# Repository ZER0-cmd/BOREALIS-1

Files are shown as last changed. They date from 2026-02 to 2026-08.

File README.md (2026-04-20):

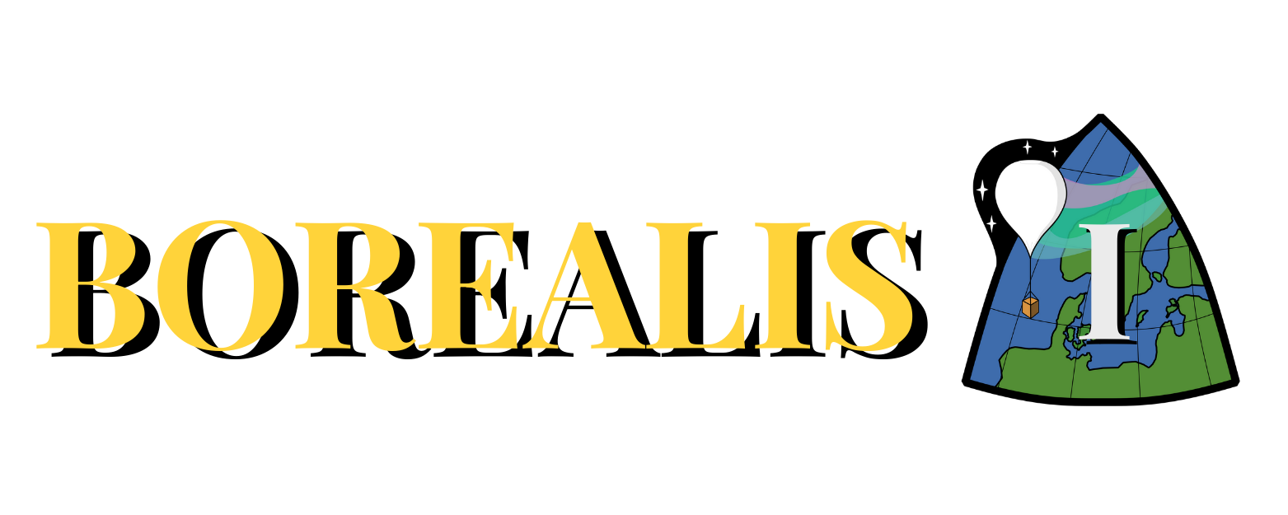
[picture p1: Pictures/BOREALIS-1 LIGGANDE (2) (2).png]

# Från klassrummen till rymden, en röd tråd från nyfikenhet till framtidens ingenjörer!
BOREALIS är ett projekt för högstadieelever som syftar till att introducera unga till teknik och rymdforskning genom praktiska, rymdnära experiment anpassade till deras kunskapsnivå. Genom att designa och bygga små experiment som skickas upp med stratosfäriska ballonger får eleverna uppleva ett verkligt rymdprojekt, vilket ger dem en första inblick i rymdteknik och ingenjörskonst. Projektet är utformat för att passa den grundläggande förståelse för naturvetenskap som elever på högstadiet har, och fungerar som en inspirerande introduktion till STEM-ämnen och framtida rymdrelaterade projekt.

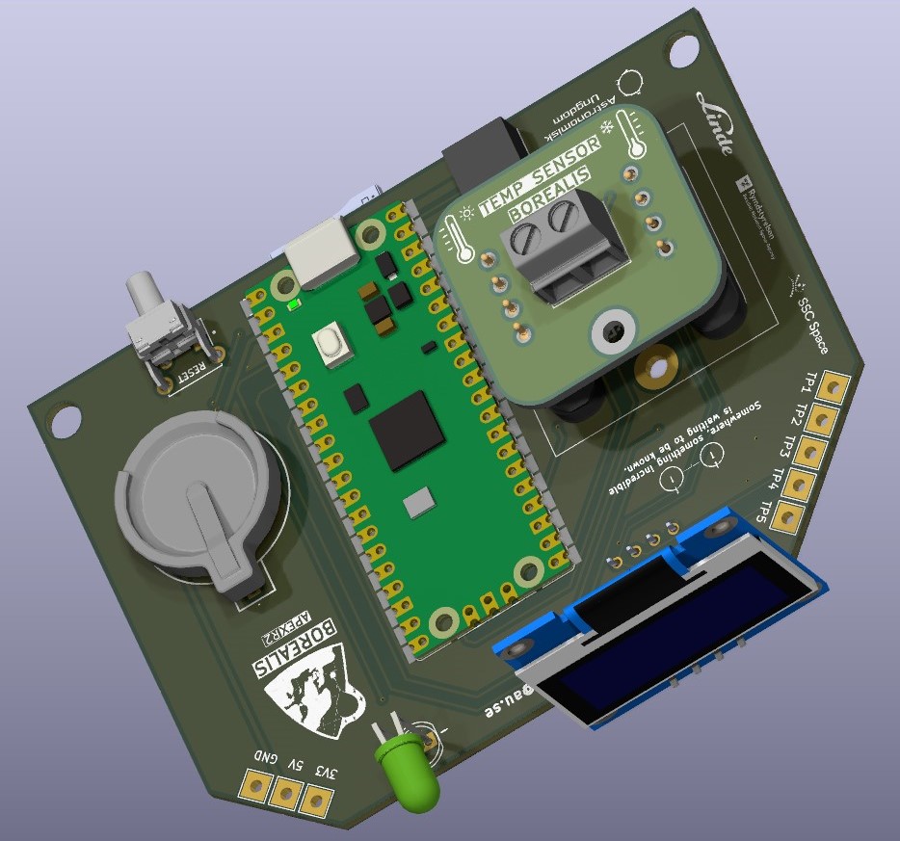
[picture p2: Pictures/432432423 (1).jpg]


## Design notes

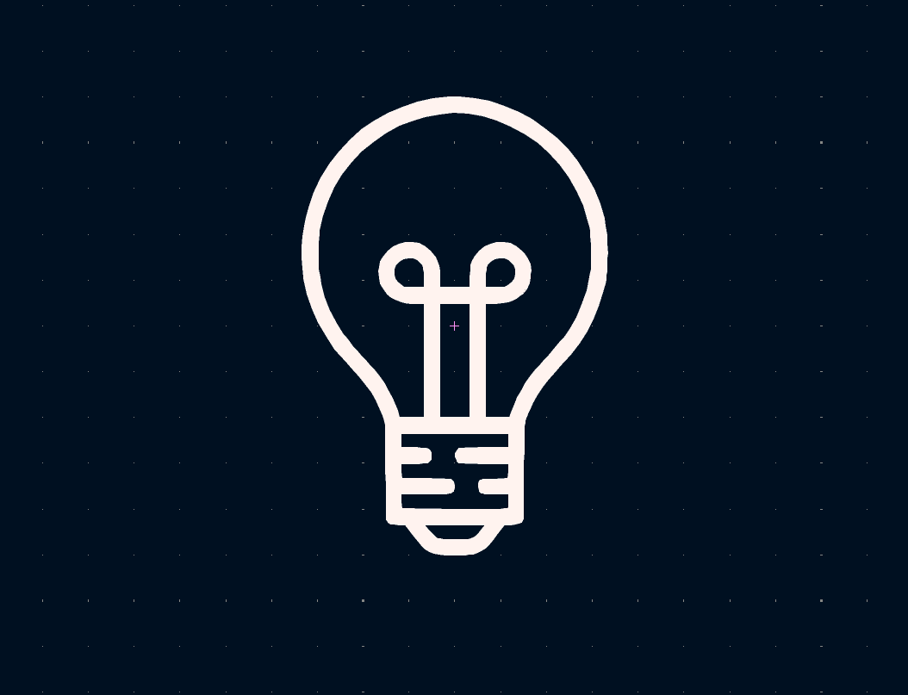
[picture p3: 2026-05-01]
Pictures/Internal/Light sensor.png

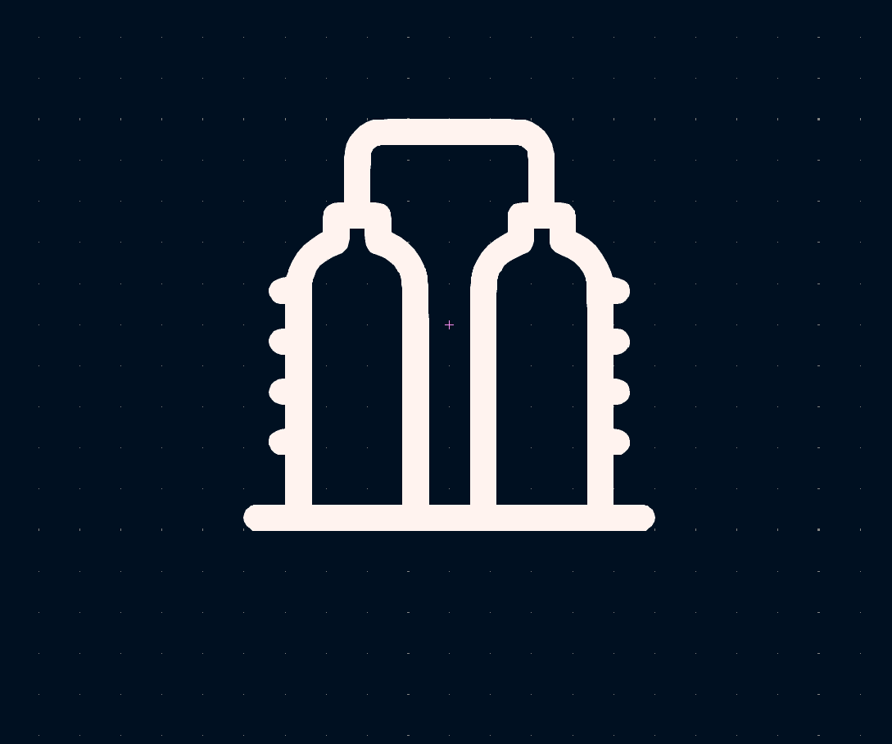
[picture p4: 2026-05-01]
Pictures/Internal/Gas sensor.png

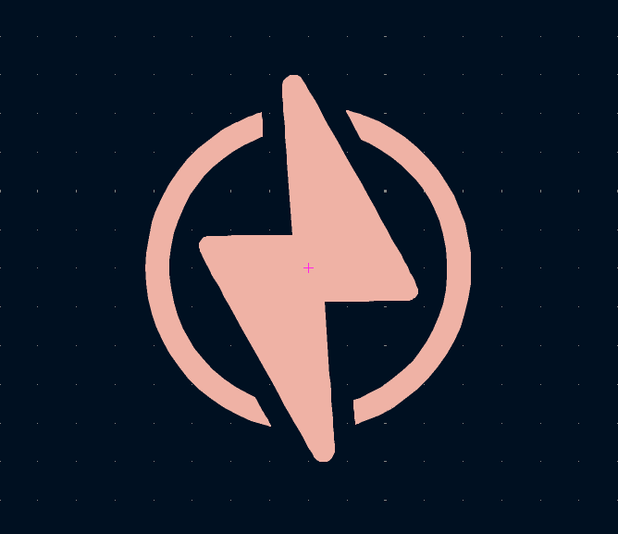
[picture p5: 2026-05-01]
Pictures/Internal/Solar panel.png

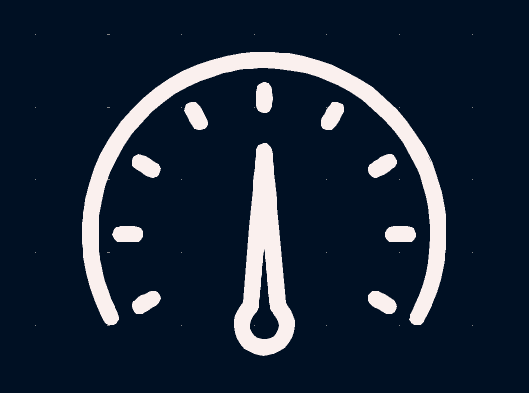
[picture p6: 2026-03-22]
Pictures/Internal/Barometer.png

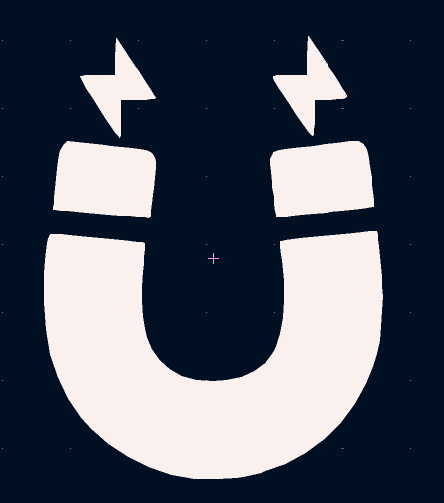
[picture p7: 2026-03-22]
Pictures/Internal/Magnetometer.png

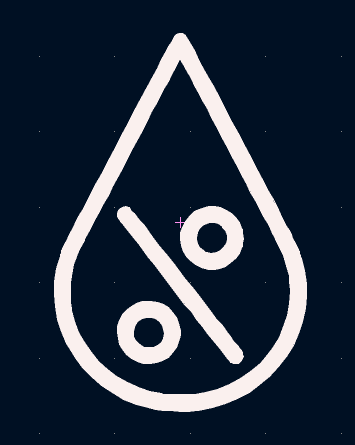
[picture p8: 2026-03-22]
Pictures/Internal/Humidity sensor.png

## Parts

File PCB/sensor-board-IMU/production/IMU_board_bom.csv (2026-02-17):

Designator | Footprint | Quantity | Value | LCSC Part #
C1, C5 | 0805 | 2 | 0.1uF
C2 | 0805 | 1 | 10nF
MPU6500 | mpu6500 | 1 | ~
R1 | 0805 | 1 | R
R2, R3 | 0805 | 2 | 4.7k
U1, U2 | MAGNETIC POGO CONN. | 2 | MAGNETIC POGO CONN.

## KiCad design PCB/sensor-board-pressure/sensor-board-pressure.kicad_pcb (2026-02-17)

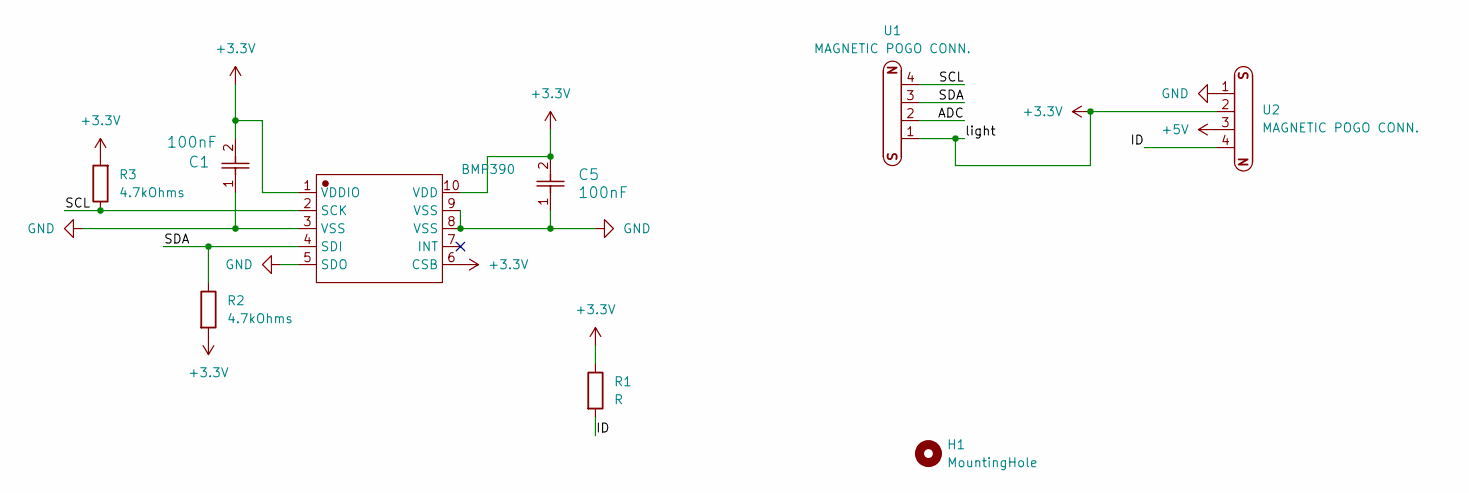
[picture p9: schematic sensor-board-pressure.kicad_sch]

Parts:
BMP390: BMP388
C1, C5: 100nF; C_0805_2012Metric
H1: MountingHole; MountingHole_2.7mm_M2.5_Pad
R1: R; R_0805_2012Metric
R2, R3: 4.7kOhms; R_0805_2012Metric
U1, U2: MAGNETIC POGO CONN.

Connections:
+3.3V: BMP390.1 (VDDIO), BMP390.6 (CSB), BMP390.10 (VDD), C1.2, C5.2, R1.1, R2.2, R3.2, U1.1, U2.2
+5V: U2.3
/ADC: U1.2
/ID: R1.2, U2.4
/SCL: BMP390.2 (SCK), R3.1, U1.4
/SDA: BMP390.4 (SDI), R2.1, U1.3
GND: BMP390.3 (VSS), BMP390.5 (SDO), BMP390.8 (VSS), BMP390.9 (VSS), C1.1, C5.1, U2.1

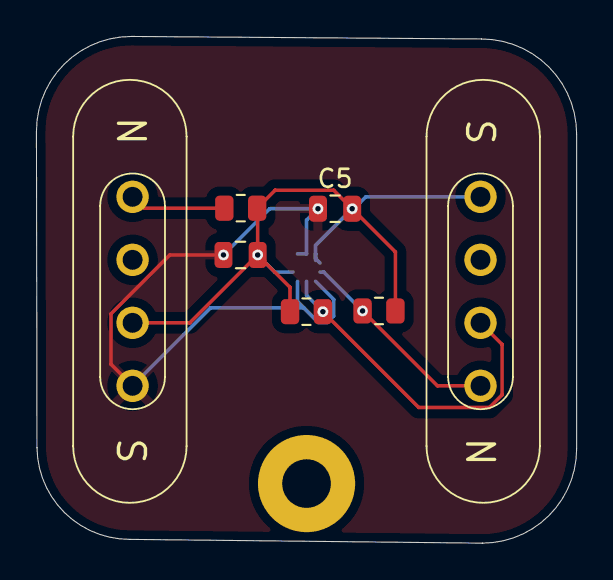
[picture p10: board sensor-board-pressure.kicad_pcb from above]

Board: 2 copper layers, 30.0 x 28.1 mm, 9 parts (1 on the bottom side), 5 nets.

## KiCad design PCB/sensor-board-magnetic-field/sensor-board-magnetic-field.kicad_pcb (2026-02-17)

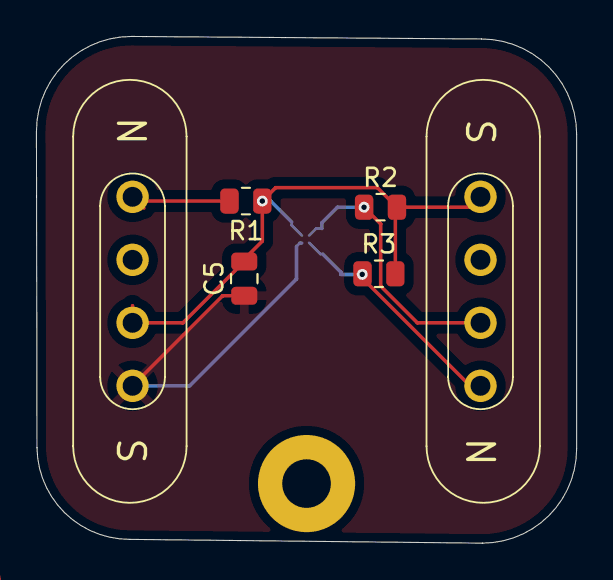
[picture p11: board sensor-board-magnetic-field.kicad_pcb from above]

Board: 2 copper layers, 30.0 x 28.1 mm, 8 parts (1 on the bottom side), 5 nets.

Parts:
C5: 2.2uf; C_0805_2012Metric
H1: MountingHole; MountingHole_2.7mm_M2.5_Pad
MMC5603NJ1: XDCR_MMC5603NJ
R1: R; R_0805_2012Metric
R2, R3: 2.7k; R_0805_2012Metric
U1, U2: MAGNETIC POGO CONN.

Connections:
+3.3V: C5.2, MMC5603NJ1.B1 (VDD), R1.1, R2.2, R3.2, U1.1, U2.2
/ID: R1.2, U2.4
/SCL: MMC5603NJ1.A2 (SCL), R3.1, U1.4
/SDA: MMC5603NJ1.B2 (SDA), R2.1, U1.3
GND: C5.1, MMC5603NJ1.A1 (VSA), U2.1

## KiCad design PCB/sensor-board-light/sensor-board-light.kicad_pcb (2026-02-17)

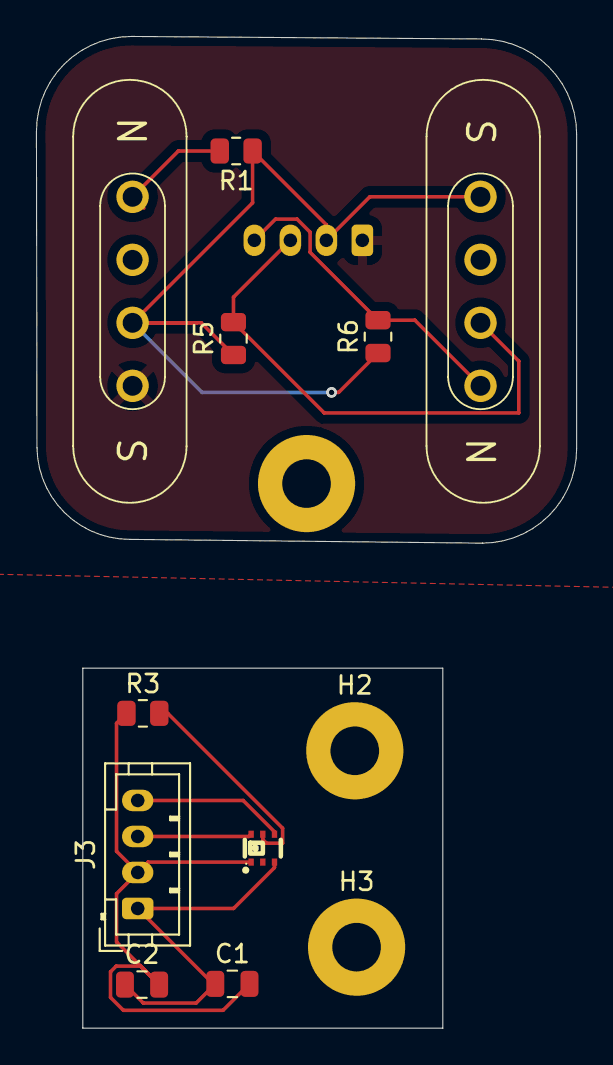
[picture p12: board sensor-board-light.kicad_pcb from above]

Board: 2 copper layers, 30.0 x 55.1 mm, 14 parts (1 on the bottom side), 9 nets.

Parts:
C1: 0.1uF; C_0805_2012Metric
C2: 4.7uF; C_0805_2012Metric
H1, H2, H3: MountingHole; MountingHole_2.7mm_M2.5_Pad
J1, J3: Conn_01x04_Pin; JST_PH_B4B-PH-K_1x04_P2.00mm_Vertical
LTR-390UV-01: SENSOR-SMD_LTR-390UV-01
R1: R; R_0805_2012Metric
R3, R5, R6: 10k; R_0805_2012Metric
U1, U2: MAGNETIC POGO CONN.

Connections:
+3.3V: J1.2, R1.1, R5.1, R6.1, U1.1, U2.2
/3.3v: C1.2, C2.2, J3.2, LTR-390UV-01.1 (VDD), R3.1
/ID: R1.2, U2.4
/SCL: J1.4, R6.2, U1.4
/SCL1: J3.4, LTR-390UV-01.4 (SCL)
/SDA: J1.3, R5.2, U1.3
/SDA1: J3.3, LTR-390UV-01.6 (SDA)
GND: C1.1, C2.1, J1.1, J3.1, LTR-390UV-01.3 (GND), U2.1
unnamed: LTR-390UV-01.5 (INT), R3.2

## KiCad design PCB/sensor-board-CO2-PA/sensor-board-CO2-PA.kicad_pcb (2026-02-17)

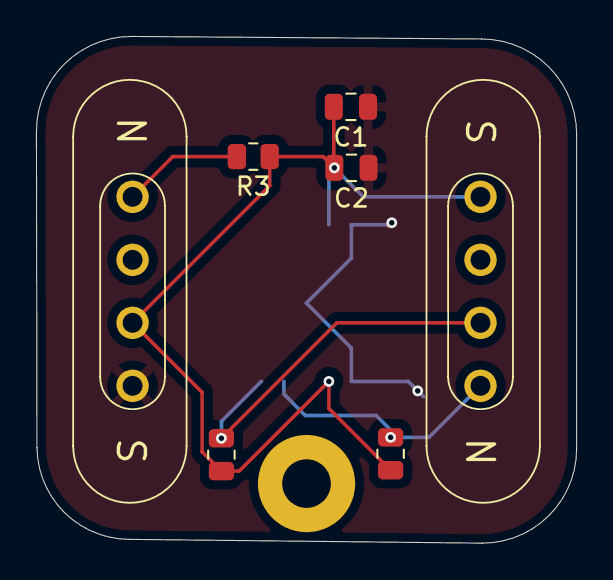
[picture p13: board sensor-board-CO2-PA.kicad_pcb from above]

Board: 2 copper layers, 30.0 x 28.2 mm, 9 parts (1 on the bottom side), 5 nets.

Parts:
C1: 10microf; C_0805_2012Metric
C2: 0.1uf; C_0805_2012Metric
H1: MountingHole; MountingHole_2.7mm_M2.5_Pad
R1: 10K; R_0805_2012Metric
R2: 10k; R_0805_2012Metric
R3: R; R_0805_2012Metric
U1, U2: MAGNETIC POGO CONN.
U1#2: SCD40-D-R2; SCD40 footprint

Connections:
+3.3V: C1.2, C2.2, R1.1, R2.1, R3.1, U1.1, U1#2.7 (VDD), U1#2.19 (VDDH), U2.2
/ID: R3.2, U2.4
/SCL: R2.2, U1.4, U1#2.9 (SCL)
/SDA: R1.2, U1.3, U1#2.10 (SDA)
GND: C1.1, C2.1, U1#2.6 (GND), U1#2.20 (GND), U1#2.21 (GND), U2.1

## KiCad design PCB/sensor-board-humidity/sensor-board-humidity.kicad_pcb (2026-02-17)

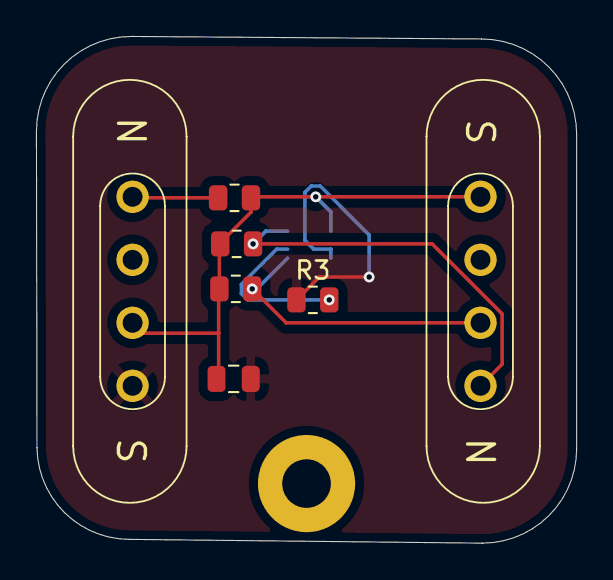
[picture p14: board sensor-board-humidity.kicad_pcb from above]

Board: 2 copper layers, 30.0 x 28.1 mm, 9 parts (1 on the bottom side), 6 nets.

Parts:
C5: 100nf; C_0805_2012Metric
H1: MountingHole; MountingHole_2.7mm_M2.5_Pad
R1: R; R_0805_2012Metric
R3, R4, R5: 10k; R_0805_2012Metric
SHT31: sht31-footprint
U1, U2: MAGNETIC POGO CONN.

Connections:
+3.3V: C5.1, R1.1, R4.1, R5.2, SHT31.5 (VDD), U1.1, U2.2
/ID: R1.2, U2.4
/SCL: R4.2, SHT31.4 (SCL), U1.4
/SDA: R5.1, SHT31.1 (SDA), U1.3
GND: C5.2, R3.1, SHT31.7 (R), SHT31.8 (VSS), SHT31.9 (EP), U2.1
unnamed: R3.2, SHT31.2 (ADDR)

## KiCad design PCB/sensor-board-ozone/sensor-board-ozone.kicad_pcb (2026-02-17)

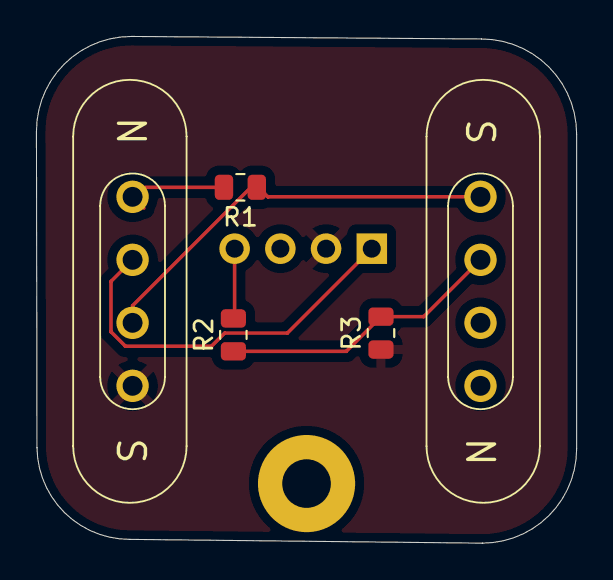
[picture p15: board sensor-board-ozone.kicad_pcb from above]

Board: 2 copper layers, 30.0 x 28.2 mm, 7 parts (1 on the bottom side), 6 nets.

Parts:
H1: MountingHole; MountingHole_2.7mm_M2.5_Pad
J2: Conn_01x04_Pin (MQ series sensor. 4pins (5v, gnd,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; PinHeader_1x04_P2.54mm_Vertical
R1, R2, R3: R; R_0805_2012Metric
U1, U2: MAGNETIC POGO CONN.

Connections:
+3.3V: R1.1, U1.1, U2.2
+5V: J2.1, U2.3
/ADC: R2.1, R3.2, U1.2
/ID: R1.2, U2.4
GND: J2.2, R3.1, U2.1
unnamed: J2.4, R2.2

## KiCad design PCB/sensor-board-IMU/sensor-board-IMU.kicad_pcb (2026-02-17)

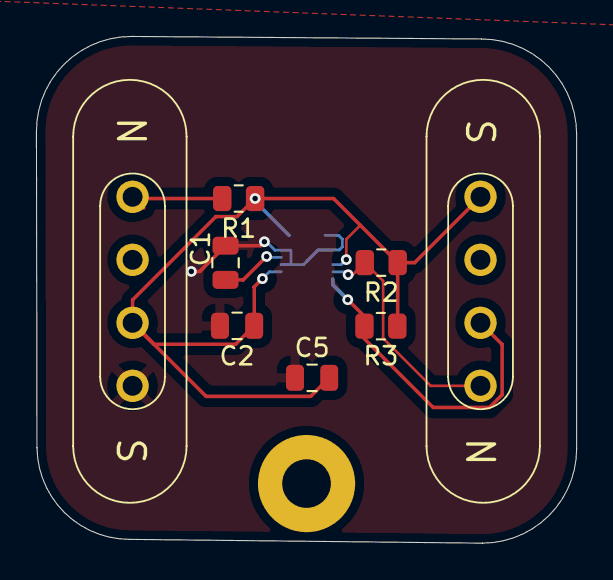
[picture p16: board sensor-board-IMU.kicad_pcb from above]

Board: 2 copper layers, 30.0 x 28.1 mm, 10 parts (1 on the bottom side), 6 nets.

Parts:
C1: 0.1uF; C_0805_2012Metric
C2: 10nF; C_0805_2012Metric
C5: 0.1uf; C_0805_2012Metric
H1: MountingHole; MountingHole_2.7mm_M2.5_Pad
MPU6500: mpu6500
R1: R; R_0805_2012Metric
R2, R3: 4.7k; R_0805_2012Metric
U1, U2: MAGNETIC POGO CONN.

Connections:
+3.3V: C2.1, C5.2, MPU6500.8 (VDDIO), MPU6500.13 (VDD), MPU6500.22 (nCS), R1.1, R2.1, R3.1, U1.1, U2.2
/ID: R1.2, U2.4
/SCL: MPU6500.23 (SCL/SCLK), R2.2, U1.4
/SDA: MPU6500.24 (SDA/SDI), R3.2, U1.3
GND: C1.2, C2.2, C5.1, MPU6500.9 (SDO/AD0), MPU6500.11 (FSYNC), MPU6500.18 (GND), MPU6500.20 (RESV), MPU6500.25 (EP), U2.1
unnamed: C1.1, MPU6500.10 (REGOUT)

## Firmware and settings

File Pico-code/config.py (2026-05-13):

# config.py - central hardware + app settings for Pico project

# OLED
OLED_WIDTH = 128
OLED_HEIGHT = 64
OLED_I2C_ADDR = 0x3C
OLED_SPLASH_MS = 3000

# OLED / RTC bus
# GP0 = SDA, GP1 = SCL
I2C_ID = 0
I2C_SDA = 0
I2C_SCL = 1
I2C_FREQ = 400_000

# DS1302 RTC (3-wire serial: CLK, DAT, CE)
# Assign to free GPIO pins on your board
DS1302_CLK = 20
DS1302_DAT = 21
DS1302_CE  = 22

# microSD detect
SD_DETECT_PIN = 19
SD_DETECT_ACTIVE_LOW = True

# Button / switch
BUTTON_PIN = 15
BUTTON_PULL = "down"
BUTTON_ACTIVE_LEVEL = 1
BUTTON_DEBOUNCE_MS = 50

# One status LED
STATUS_LED_PIN = 2
LED_ACTIVE_HIGH = True

# SD Card (SPI1)
SD_SPI_ID = 1
SD_SCK = 10
SD_MOSI = 11 #RX
SD_MISO = 8 #TX
SD_CS = 9
SD_BAUDRATE = 1_000_000
SD_MOUNT_POINT = "/sd"

# Sampling / UI update
SAMPLE_INTERVAL_MS = 1000

# Sensor identification ADC
SENSOR_ID_ADC_PIN = 28

# Sensor bus (from your working test scripts)
SENSOR_I2C_ID = 1
SENSOR_I2C_SDA = 14
SENSOR_I2C_SCL = 15
SENSOR_I2C_FREQ = 100_000

# ADC bus (i2c0 on schematic)
ADC_I2C_ID = 0
ADC_I2C_SDA = 0
ADC_I2C_SCL = 1
ADC_I2C_FREQ = 400_000
ADC_CHANNEL = 2


# CO2 | 680 Ω
# BAR | 510 Ω
# light | 750 Ω
# GAS | 560 Ω
# HUM | 1.1 kΩ
# VOLT | 820 Ω
# TEMP | 1.2 kΩ
# MAG | 910 Ω
# ACL | 620 Ω

# Formula:
# V = 6.6e7 / (R + 1000)

# Sensor ID ranges
SENSOR_NONE_ID = 0
SENSOR_CO2_ID = 39355
SENSOR_PRESSURE_ID = 43354
SENSOR_LIGHT_ID = 37800
SENSOR_GAS_ID = 42314
SENSOR_HUMIDITY_ID = 31518
SENSOR_SOLAR_ID = 36263
SENSOR_TEMP_ID = 30136
SENSOR_MAGNETOMETER_ID = 34645
SENSOR_MPU6500_ID = 40841

UV_RESOLUTION = 18

# Timing
SENSOR_ANNOUNCE_MS = 2000
SENSOR_READ_INTERVAL_MS = 1000

# Reset pin
RESET1_PIN = 17
RESET2_PIN = 6

DEFAULT_FILE_NAME = 'data.csv'

LED_GREEN = 3
LED_BLUE = 4

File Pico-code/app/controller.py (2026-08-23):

import time
from machine import Pin, I2C, SPI, reset
import config
from drivers.display_ssd1306 import SSD1306_I2C
from drivers.output_led import LED
from drivers.sd_detect import SdDetect
from app.timekeeping import Timekeeper
from app.ui import Ui
from app import logging
from app.sensor_manager import (
    SensorManager,
    SENSOR_NONE,
    SENSOR_HUMIDITY,
    SENSOR_PRESSURE,
    SENSOR_MPU6500,
    SENSOR_UNKNOWN,
    SENSOR_GAS,
    SENSOR_LIGHT,
    SENSOR_SOLAR,
    SENSOR_TEMP,
    SENSOR_MAGNET,
    SENSOR_NAMES,
)


class Core(Timekeeper):
    def __init__(self):
        self.green_led = LED(
            config.LED_GREEN,
            active_high=config.LED_ACTIVE_HIGH,
        )
        self.blue_led = LED(
            config.LED_BLUE,
            active_high=config.LED_ACTIVE_HIGH,
        )
        self.status_led = LED(
            config.STATUS_LED_PIN,
            active_high=config.LED_ACTIVE_HIGH,
        )
        self.reset1 = Pin(config.RESET1_PIN, Pin.IN, Pin.PULL_DOWN)
        self.reset2 = Pin(config.RESET2_PIN, Pin.IN, Pin.PULL_DOWN)
        self.i2c = I2C(
            config.I2C_ID,
            sda=Pin(config.I2C_SDA),
            scl=Pin(config.I2C_SCL),
            freq=config.I2C_FREQ,
        )
        self.oled = None
        self.sd_detect = SdDetect(
            config.SD_DETECT_PIN,
            active_low=config.SD_DETECT_ACTIVE_LOW,
        )
        self.sd = None
        self.sensor_manager = SensorManager(i2c_adc=self.i2c)
        self.last_sensor_read_ms = 0
        self.log_ready = False
        self.data = {}
        self.datakeys = []
        self.sensorkeys = []
        self.ui = None
        self.filter = []

        self.dataready = False

        Timekeeper.__init__(self)

    def _run_startup_checks(self):
        start_ms = time.ticks_ms()
        splash_ms = config.OLED_SPLASH_MS
        led_state = False
        last_toggle_ms = start_ms
        blink_interval_ms = 100
        sd_ok = False
        while time.ticks_diff(time.ticks_ms(), start_ms) < splash_ms:
            now = time.ticks_ms()
            sd_ok = self.sd_detect.is_inserted()
            if time.ticks_diff(now, last_toggle_ms) >= blink_interval_ms:
                last_toggle_ms = now
                led_state = not led_state
                if led_state:
                    self.status_led.on()
                else:
                    self.status_led.off()
            time.sleep_ms(10)
        return sd_ok

    def _show_check_result(self, ok):
        if ok:
            self.status_led.off()
            time.sleep_ms(80)
            self.status_led.on()
            time.sleep_ms(200)
            self.status_led.off()
            time.sleep_ms(120)
            self.status_led.on()
        else:
            self.status_led.off()

    def _oledmanager(self):
        if self.ui is not None:
            self.oled = self.ui.oled
        if self.oled is not None:
            return
        if config.OLED_I2C_ADDR in self.i2c.scan():
            try:
                self.oled = SSD1306_I2C(
                    config.OLED_WIDTH,
                    config.OLED_HEIGHT,
                    self.i2c,
                    addr=config.OLED_I2C_ADDR,
                )
            except Exception as e:
                print("OLED init failed:", e)
                self.oled = None
        self.ui = Ui(self.oled)
        self.oled = self.ui.oled

    def _experimentmanager(self):
        self.changed, kind, adc_value = self.sensor_manager.refresh_connection()
        if self.changed:
            if kind == SENSOR_NONE:
                self.ui.show_sensor_disconnected()
                self.ui.show()
                time.sleep_ms(config.SENSOR_ANNOUNCE_MS)
            elif kind == SENSOR_UNKNOWN:
                self.ui.show_unknown_sensor(adc_value)
                self.ui.show()
                time.sleep_ms(config.SENSOR_ANNOUNCE_MS)
            else:
                self.ui.show_sensor_connected(SENSOR_NAMES[kind])
                self.ui.show()
                time.sleep_ms(config.SENSOR_ANNOUNCE_MS)

            self.filter = []

        now = time.ticks_ms()
        if time.ticks_diff(now, self.last_sensor_read_ms) >= config.SENSOR_READ_INTERVAL_MS:
            self.last_sensor_read_ms = now
            self.data = self.sensor_manager.read_data()
            if self.data is None:
                self.ui.show_sensor_disconnected()
                self.dataready = False
                return
            if self.data["kind"] == SENSOR_HUMIDITY:
                self.sensorkeys = ["humidity_percent"]
                show = self.ui.show_humidity_data
            elif self.data["kind"] == SENSOR_PRESSURE:
                self.sensorkeys = ["pressure_hpa"]
                show = self.ui.show_pressure_data
            elif self.data["kind"] == SENSOR_MPU6500:
                self.sensorkeys = ["ax_g", "ay_g", "az_g", "gx_dps", "gy_dps", "gz_dps"]
                show = self.ui.show_mpu6500_data
            elif self.data["kind"] == SENSOR_SOLAR:
                self.sensorkeys = ["voltage"]
                show = self.ui.show_solar_data
            elif self.data["kind"] == SENSOR_TEMP:
                self.sensorkeys = ["temperature_c"]
                show = self.ui.show_temp_data
            elif self.data["kind"] == SENSOR_GAS:
                self.sensorkeys = ["alcohol"]
                show = self.ui.show_gas_data
            elif self.data["kind"] == SENSOR_LIGHT:
                self.sensorkeys = ["uvindex"]
                show = self.ui.show_light_data
            elif self.data["kind"] == SENSOR_MAGNET:
                self.sensorkeys = ["B_x", "B_y", "B_z"]
                show = self.ui.show_magnet_data
            else:
                self.ui.show_unknown_sensor(self.data["adc"])
                self.dataready = False
                return

            self.data["elapsed_s"] = self.elapsed_s()
            self.data['datetime'] = self.fdate()
            self.datakeys = ['datetime', "elapsed_s"] + self.sensorkeys
            if self.filter == []:
                self.filter = self.sensorkeys

            if self.cdata is not None:
                kind = self.data["kind"]
                if kind in self.cdata:
                    c = self.cdata[kind]
                    for k, (scale, shift) in c.items():
                        if k in self.data:
                            self.data[k] = self.data[k] * scale + shift

            show(*(self.data[k] for k in self.sensorkeys))

            self.dataready = True
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

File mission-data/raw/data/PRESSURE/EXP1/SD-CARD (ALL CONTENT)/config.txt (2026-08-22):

# For more options and information see
# http://rptl.io/configtxt
# Some settings may impact device functionality. See link above for details

# Uncomment some or all of these to enable the optional hardware interfaces
#dtparam=i2c_arm=on
#dtparam=i2s=on
dtparam=spi=on

# Enable audio (loads snd_bcm2835)
dtparam=audio=on

# Additional overlays and parameters are documented
# /boot/firmware/overlays/README

# Automatically load overlays for detected cameras
camera_auto_detect=1

# Automatically load overlays for detected DSI displays
display_auto_detect=1

# Automatically load initramfs files, if found
auto_initramfs=1

# Enable DRM VC4 V3D driver
dtoverlay=vc4-kms-v3d
max_framebuffers=2

# Don't have the firmware create an initial video= setting in cmdline.txt.
# Use the kernel's default instead.
disable_fw_kms_setup=1

# Run in 64-bit mode
arm_64bit=1

# Disable compensation for displays with overscan
disable_overscan=1

# Run as fast as firmware / board allows
arm_boost=1

[cm4]
# Enable host mode on the 2711 built-in XHCI USB controller.
# This line should be removed if the legacy DWC2 controller is required
# (e.g. for USB device mode) or if USB support is not required.
otg_mode=1

[cm5]
dtoverlay=dwc2,dr_mode=host

[pi5]
dtoverlay=nospi10

[all]
enable_uart=1

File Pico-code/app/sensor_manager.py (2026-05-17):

from machine import ADC, Pin, I2C
import time
import config
import gc

from drivers.sensor_sht31 import SHT31

from drivers.bmp390 import BMP390
from drivers.mpu6500 import MPU6500
from drivers.ADS1115 import ADS1115
from drivers.mmc5603 import MMC5603
from drivers import ltr390


SENSOR_NONE = config.SENSOR_NONE_ID
SENSOR_CO2 = config.SENSOR_CO2_ID
SENSOR_HUMIDITY = config.SENSOR_HUMIDITY_ID
SENSOR_PRESSURE = config.SENSOR_PRESSURE_ID
SENSOR_MPU6500 = config.SENSOR_MPU6500_ID
SENSOR_LIGHT = config.SENSOR_LIGHT_ID 
SENSOR_GAS = config.SENSOR_GAS_ID
SENSOR_SOLAR = config.SENSOR_SOLAR_ID
SENSOR_TEMP = config.SENSOR_TEMP_ID
SENSOR_MAGNET = config.SENSOR_MAGNETOMETER_ID
SENSOR_UNKNOWN = "unknown"

SENSOR_NAMES = {
    SENSOR_NONE : "No sensor",
    SENSOR_HUMIDITY : 'Humidity sensor',
    SENSOR_PRESSURE : 'Barometer',
    SENSOR_MPU6500 : 'Accelerometer',
    SENSOR_LIGHT : 'Light sensor',
    SENSOR_GAS : 'Gas sensor',
    SENSOR_SOLAR : 'Solar panel',
    SENSOR_TEMP : 'Termometer',
    SENSOR_CO2 : 'CO2 sensor',
    SENSOR_MAGNET : 'Magnetometer',
    SENSOR_UNKNOWN : "Unknown sensor"
}

class SensorManager:
    def __init__(self, i2c_adc=None):
        self.adc = ADC(config.SENSOR_ID_ADC_PIN)

        self.i2c = I2C(
            config.SENSOR_I2C_ID,
            sda=Pin(config.SENSOR_I2C_SDA),
            scl=Pin(config.SENSOR_I2C_SCL),
            freq=config.SENSOR_I2C_FREQ,
        )

        if i2c_adc is not None:
            self.i2c_adc = i2c_adc
        else:
            self.i2c_adc = I2C(
                config.ADC_I2C_ID,
                sda=Pin(config.ADC_I2C_SDA),
                scl=Pin(config.ADC_I2C_SCL),
                freq=config.ADC_I2C_FREQ,
            )

        self.current_kind = None
        self.sensor = None
        self._pending = None
        self._pcount = 0

    def read_adc(self): # ID
        return self.adc.read_u16()
    
    def _adc(self): # Actual ADC
        return self.sensor.read_voltage(config.ADC_CHANNEL)
    
    @staticmethod
    def classify(adc_value):
        closest = min([SENSOR_NONE, SENSOR_GAS, SENSOR_HUMIDITY, SENSOR_LIGHT, SENSOR_MPU6500, SENSOR_PRESSURE, SENSOR_SOLAR, SENSOR_TEMP, SENSOR_CO2, SENSOR_MAGNET], key=lambda x : abs(x-adc_value))
        if abs(adc_value - closest) > 3000:
            return SENSOR_UNKNOWN
        return closest

    def connect_for_kind(self, kind):
        self.sensor = None
        self.current_kind = kind
        gc.collect()

        time.sleep_ms(20)
        if kind == SENSOR_NONE:
            return
        try:
            if kind == SENSOR_HUMIDITY:
                self.sensor = SHT31(self.i2c)
                return

            if kind == SENSOR_PRESSURE:
                last_exc = None
                for addr in (0x77, 0x76):
                    try:
                        self.sensor = BMP390(self.i2c, address=addr)
                        return
                    except Exception as e:
                        last_exc = e
                if last_exc:
                    raise last_exc
                raise RuntimeError("BMP390 not found")

            if kind == SENSOR_MPU6500:
                last_exc = None
                for addr in (0x68, 0x69):
                    try:
                        self.sensor = MPU6500(self.i2c, address=addr)
                        return
                    except Exception as e:
                        last_exc = e
                if last_exc:
                    raise last_exc
                raise RuntimeError("MPU6500 not found")
            
            if kind == SENSOR_LIGHT:
                # note: als mode exclusive with uv
                self.sensor = ltr390.LTR390(self.i2c)
                self.gain = 1
                self.sensor.set_gain(ltr390.GAINS[self.gain])
                self.sensor.set_resolution(config.UV_RESOLUTION)
                self.sensor.enable_uv()
                time.sleep_ms(self.sensor._int_ms + 10)
                return
            
            if kind == SENSOR_MAGNET:
                self.sensor = MMC5603(self.i2c)
                self.sensor.set_resolution(0)
                self.qcal = self.sensor.read_raw()
                return
            
            if kind in (SENSOR_TEMP, SENSOR_SOLAR, SENSOR_GAS):
                self.sensor = ADS1115(self.i2c_adc)
        except Exception as e:
            self.current_kind = SENSOR_UNKNOWN
            self.sensor = None

    def refresh_connection(self):
        try:
            adc_value = self.read_adc()
            kind = self.classify(adc_value)
            
            if kind == self._pending:
                self._pcount += 1
            else:
                self._pending = kind
                self._pcount = 1

            if self._pcount >= 8 and kind != self.current_kind:
                self.connect_for_kind(kind)
                return True, kind, adc_value

            return False, kind, adc_value
        except Exception:
            return False, self.current_kind, 0

    def read_data(self):
        if self.current_kind == SENSOR_NONE:
            return None
        
        if self.current_kind == SENSOR_UNKNOWN:
            return {
                "kind": SENSOR_UNKNOWN,
                "adc": self.read_adc(),
            }

        try:
            if self.current_kind == SENSOR_HUMIDITY:
                temp_c, humidity = self.sensor.read()
                return {
                    "kind": SENSOR_HUMIDITY,
                    "temperature_c": temp_c,
                    "humidity_percent": humidity,
                }

            if self.current_kind == SENSOR_PRESSURE:
                temp_c, pressure_pa = self.sensor.read()
                return {
                    "kind": SENSOR_PRESSURE,
                    "pressure_hpa": pressure_pa / 100.0,
                    "temperature_c" : temp_c
                }

            if self.current_kind == SENSOR_MPU6500:
                ax, ay, az = self.sensor.read_accel()
                gx, gy, gz = self.sensor.read_gyro()
                temp_c = self.sensor.read_temperature()

                return {
                    "kind": SENSOR_MPU6500,
                    "temperature_c": temp_c,
                    "ax_g": ax,
                    "ay_g": ay,
                    "az_g": az,
                    "gx_dps": gx,
                    "gy_dps": gy,
                    "gz_dps": gz,
                }
            
            if self.current_kind == SENSOR_TEMP:
                v = self._adc()
                temp = (v - 1.25) / 0.005
                return {
                    "kind" : SENSOR_TEMP,
                    "temperature_c" : temp
                    }

            if self.current_kind == SENSOR_GAS:
                v = self._adc()
                return {'kind': SENSOR_GAS,
                        'alcohol': 1.5*v}
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

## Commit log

2026-02-15 Update PCB files (pressure + solar)#
    [sensor-board-CO2-PA.kicad_pcb, sensor-board-pressure.kicad_pcb, sensor-board-pressure.kicad_sch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]
2026-02-16 made some changes
    [BOREALIS_MOTHERBOARD.kicad_pcb, BOREALIS_MOTHERBOARD.kicad_sch, Borealis.kicad_pcb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]
2026-02-17 Made some final checks and changes
    [IMU_board_bom.csv, IMU_board_designators.csv, IMU_board_positions.csv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]
2026-02-22 Add files via upload
    Added sample data
    [Sweden_CH4_CO2_0_32km.csv, standard_atmosphere_si_noisy_strong.csv, stockholm_solar_irradiance_0-30km_clear_noon_equinox.csv]
2026-03-07 Update module_eng.py
    Added support for inverted y and x axis
2026-03-10 Sourced new sensor libraries
2026-03-20 UI picture support
    [logo.csv]
2026-03-21 fixed picture
    [logo.csv]
2026-03-21 Actually fixed picture
    [logo.csv]
2026-03-21 LED works now!
2026-03-21 added some sensor stuff
2026-03-21 made some sensor changes
2026-03-22 more pictures!
    [co2.csv, humidity.csv, logo.csv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]
2026-04-04 fixed ui sensor init issue
    [controller.py]
2026-04-13 flipped OLED. Improved SD logging protocol
    [controller.py, display_ssd1306.py, logging.py]
2026-04-27 Streamlined sensor idntification + added identification of more sensors
2026-04-30 Solar sensor test1
2026-05-01 Sensors!!!! (good enough)
    [Accelerometer.csv, Barometer.csv, CO2 sensor.csv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]
2026-05-17 direct firmaware incorporation + developer methods + small bug fix
    [Accelerometer.csv, Barometer.csv, CO2 sensor.csv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]
2026-06-01 Create data.csv
    fil till berzan
    [data.csv]
2026-06-01 copilot is thinking # bro is the tinker
    [borealis_mission_data.csv]
2026-06-01 del sys32
    [data.csv]
2026-06-01 Rename column 'Höjd_m' to 'Alt_m' in CSV file
    [borealis_mission_data.csv]
